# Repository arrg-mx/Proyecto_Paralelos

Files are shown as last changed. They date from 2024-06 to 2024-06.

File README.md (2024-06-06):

# Proyecto_Paralelos
En este repositorio de administrarán los proyectos y sus respectivos programas relacionados con el desarrollo e implementación de robots paralelos por cables.

- [Objetivo](#objetivo)
- [Metas](#metas)
- [Participantes](#participantes)
- [Referencias](#referencias)

## Objetivo

Implementar un robot paralelo dirigido por cables para que este pueda realizar tareas de sensado y manipulación de materiales.

## Metas

- [ ] Implementar el actuador de los cables del robot*
- [ ] Diseñar la estructura y el cuerpo del robot para su implementación en la estructura del espacio de trabajo del tercer piso.

## Participantes

**Integrantes del proyecto:**

| Nombre | Observaciones | Semestre |
| :---| :--- | :--- |
| M.I. Erik Peña Medina | **Responsable** | ---- 
| Braughton Portas Ricardo Alastair | **Participante** | 2024-2 |

## Referencias

### ¿Dónde empezar?

1. **Cable-Driven Parallel Robots**[Libro](https://link.springer.com/content/pdf/10.1007/978-3-319-76138-1.pdf).
2. **Open-Source Planar Cable-Driven Robot**[Repositorio](https://github.com/LionelBirglen/OpenSourcePlanarCableRobot/tree/main)
3. **Modelling and Implementation of Cable Driven Parallel Manipulator System with Tension Control** [Repositorio](https://github.com/siddharthumakarthikeyan/Cable-Driven-Parallel-Robots-CDPR-Modelling)
4. **Accuracy of large-scale cable-driven parallel robot with universal joint pulleys**[Articulo](https://hal.science/hal-03393239/)
5. **Cable Driven Parallel Robot**[Video](https://www.youtube.com/watch?v=cxKAWujUV-c)
6. **Digital design of a сable-driven parallel robot**[Articulo](https://iopscience.iop.org/article/10.1088/1757-899X/945/1/012085/pdf)
7. **A Deployable Cable-Driven Parallel Robot With Large Rotational Capabilities for Laser-Scanning Applications**[Articulo](https://ieeexplore.ieee.org/abstract/document/9076279)
8. **Kinematics of the wire-driven parallel robot MARIONET using linear actuators**[Articulo](https://ieeexplore.ieee.org/abstract/document/4543803)
9. **A Review of Cable-Driven Parallel Robots: Typical Configurations, Analysis Techniques, and Control Methods**[Articulo](https://ieeexplore.ieee.org/abstract/document/9745192)
10. **Design and Development of a New Cable-Driven Parallel Robot for Waist Rehabilitation**[Articulo](https://ieeexplore.ieee.org/abstract/document/8716563)
11. **Design and implementation of a cable-driven parallel robot for additive manufacturing applications**[Articulo](https://www.sciencedirect.com/science/article/abs/pii/S0957415822000964)
## Introducción
El presente proyecto tiene por objetivo el diseño, implementación y control de un robot paralelo controlado por cables para ser instalado en el tercer piso del Centro de Ingeniería Avanzada en la facultad de Ingeniería.
## Etapas de desarrollo
Este proyecto constara de las siguientes etapas de desarrollo las cuales se realizarán de manera secuencial:
1. Diseño y construcción del actuador encargado de la variación de longitud de los cables.
2. Diseño y construcción de la estructura necesaria para soportar el actuador .
3. Implementación del método de control del actuador 
...
## 1. Diseño y constrcción del actuador
Para el diseño del actuador, tras analizar los mecanismos existentes actualmente se optó por un tornillo sin fin el cual cumpla la función de un carrete para el cable conectado directamente a la flecha de un motor pololou GB37-100.  
En esta etapa se realizaron múltiples iteraciones con la finalidad de refinar el diseño.

- **Primera iteración**  
En esta iteración se imprimió el modelo con un relleno de 10% y un espesor de pared de .8mm lo cual hizo que la pieza fuera altamente frágil por lo cual ni siquiera se concluyó la impresión, sin embargo con la parte impresa al retirar los soportes la pieza fracturó reafirmando la observación sobre su fragilidad.
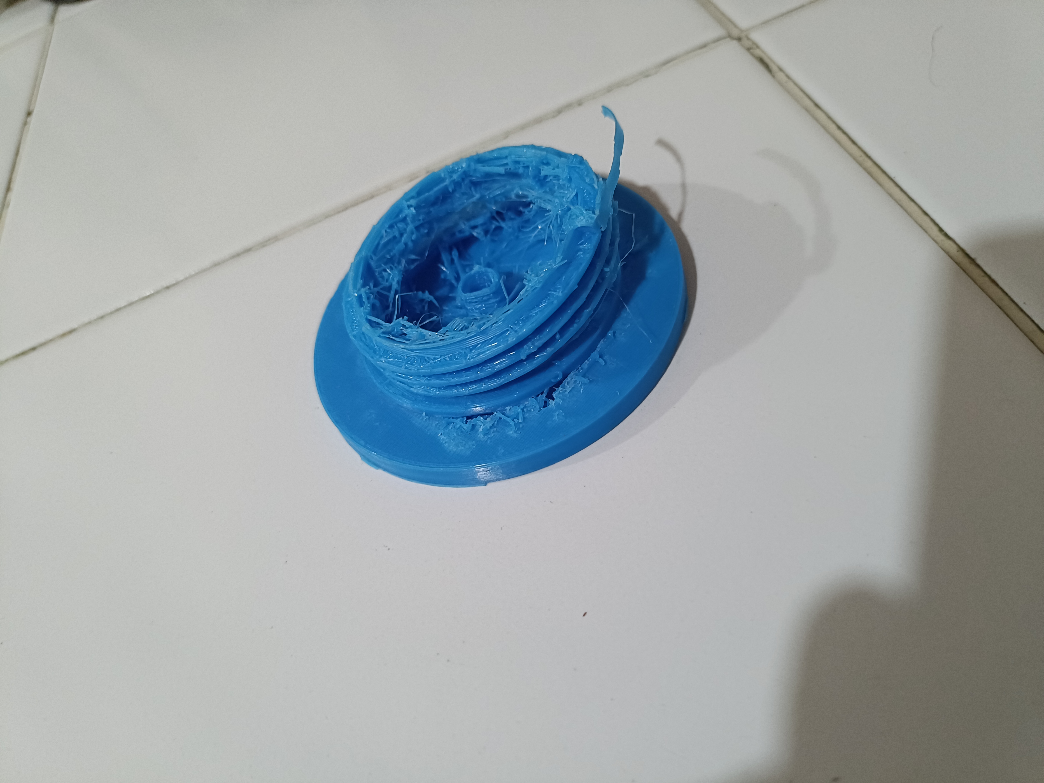
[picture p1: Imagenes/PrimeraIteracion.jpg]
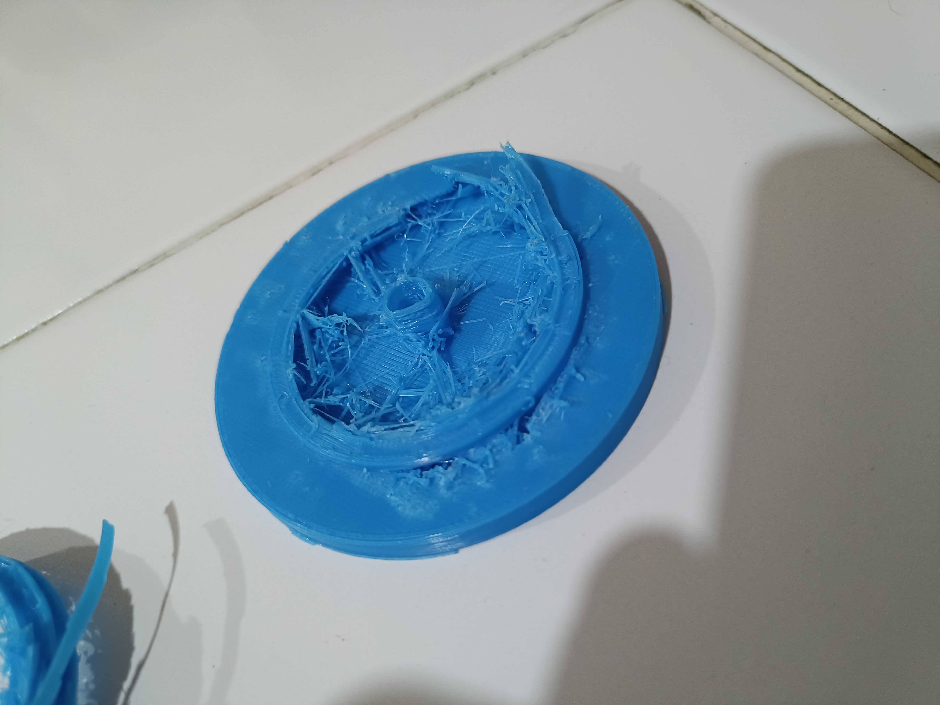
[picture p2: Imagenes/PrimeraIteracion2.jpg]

- **Segunda iteración**  
Para la segunda iteración se incrementó el relleno a un 20% y el espesor de pared a 2mm lo cual generó una pieza exitosa, sin embargo, con esta impresión nos percatamos de que el diseño del carrete no contaba con ninguna clase de soporte, por lo cual, de ser implementado las cargas normales producirían daños en la flecha del motor. Por otro lado, el barreno de la pieza que se diseñó para sostener el hilo se cerró debido a que se diseñó con un grosor muy reducido si embargo este se re-abrió fácilmente con la ayuda de una aguja caliente.
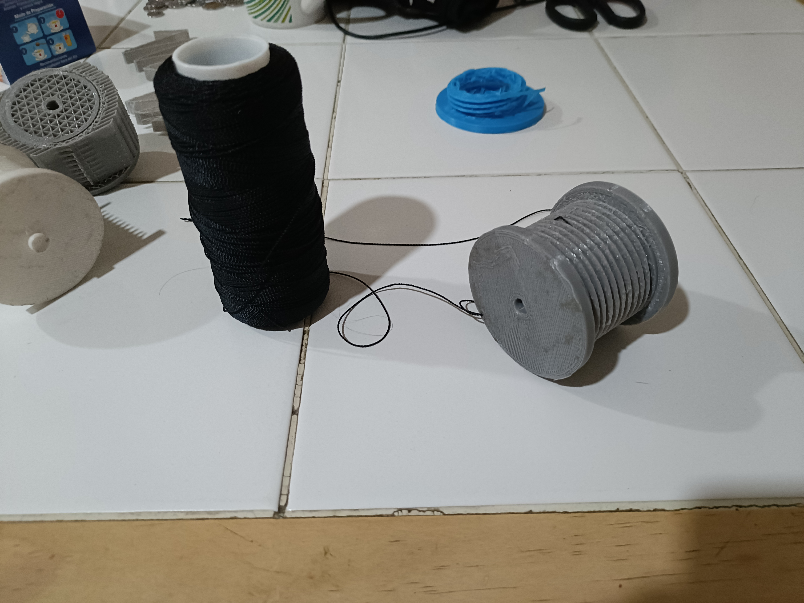
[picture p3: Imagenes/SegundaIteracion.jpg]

- **Tercera iteracion**  
En esta ocasión, tras los errores observados en la impresión pasada, se decidió colocar el carrete sobre un eje acoplado con un balero 608Z.  
Al momento de imprimir esta pieza con los mismos parámetros de impresión de las piezas anteriores, la pieza fallo debido a un corte en el suministro de luz, dejando la pieza a un 80% por lo cual la pieza no fue útil sin embargo se realizaron pruebas de ajuste del eje con el balero, pero al intentar colocar el balero el eje se rompió evidenciando que el diámetro del eje era insuficiente.
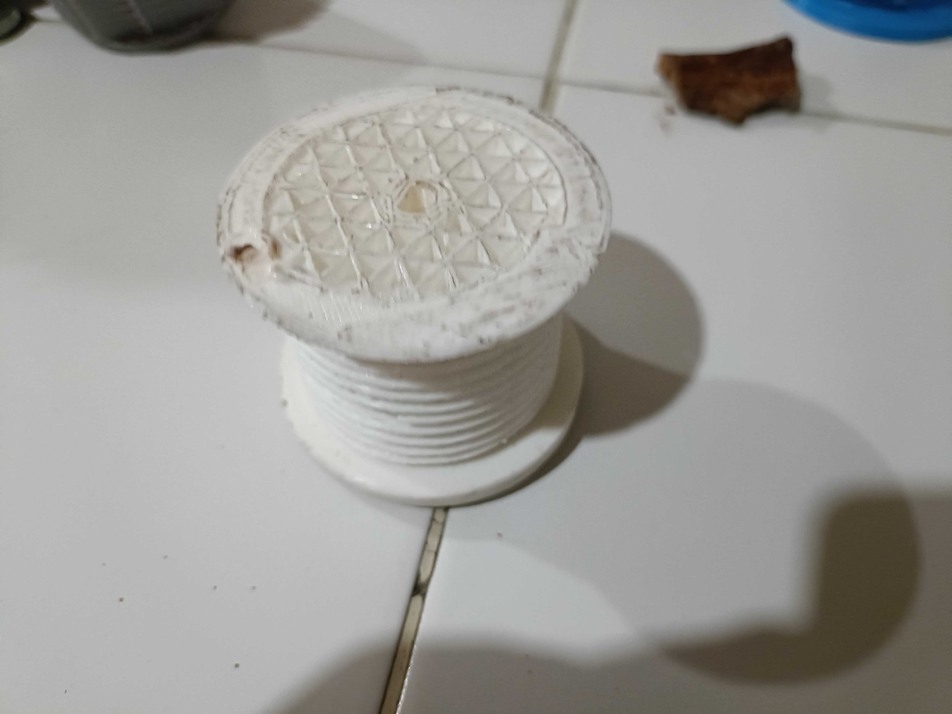
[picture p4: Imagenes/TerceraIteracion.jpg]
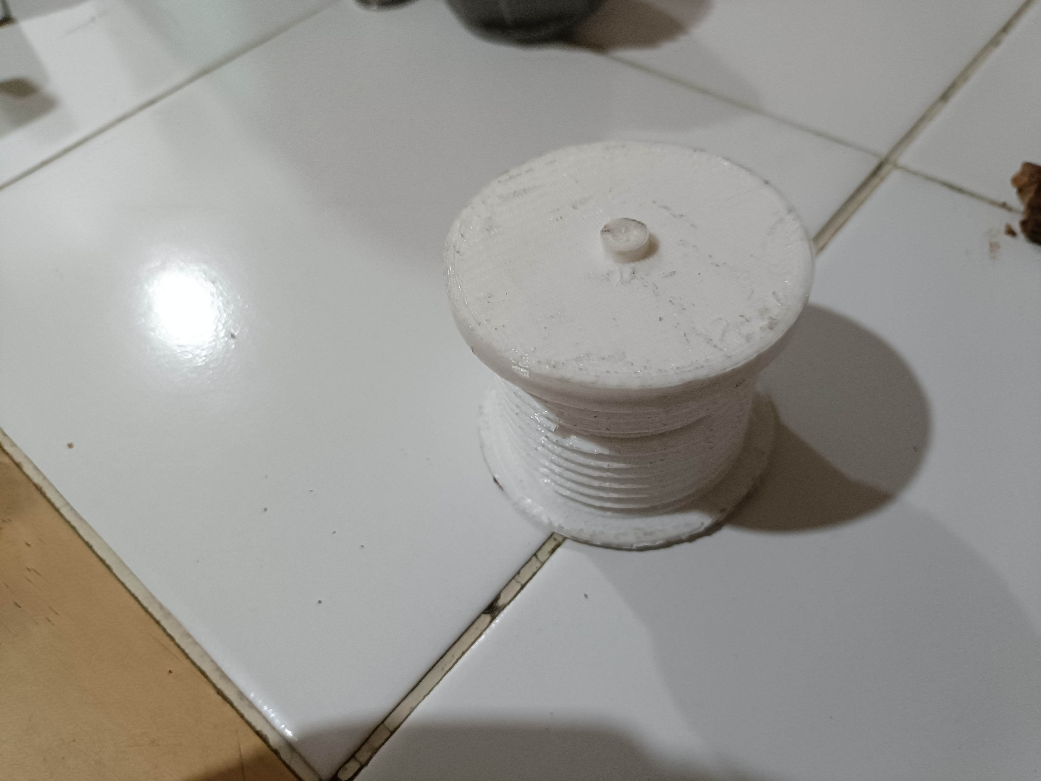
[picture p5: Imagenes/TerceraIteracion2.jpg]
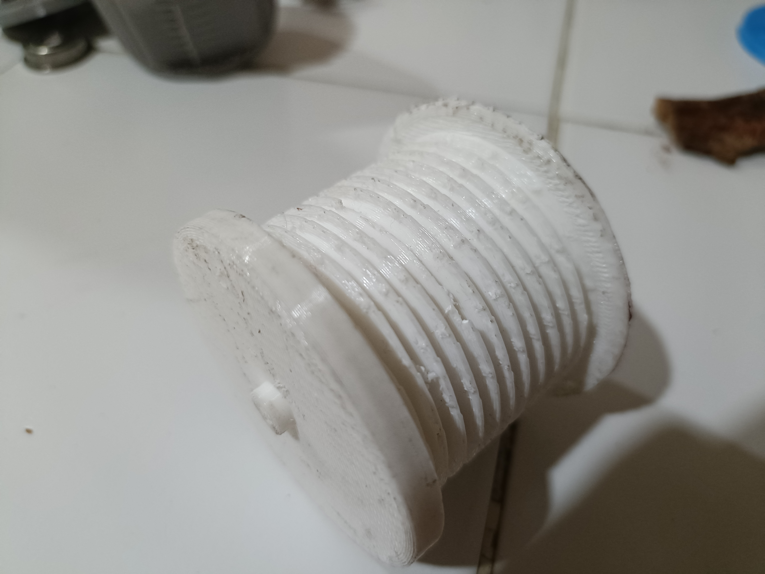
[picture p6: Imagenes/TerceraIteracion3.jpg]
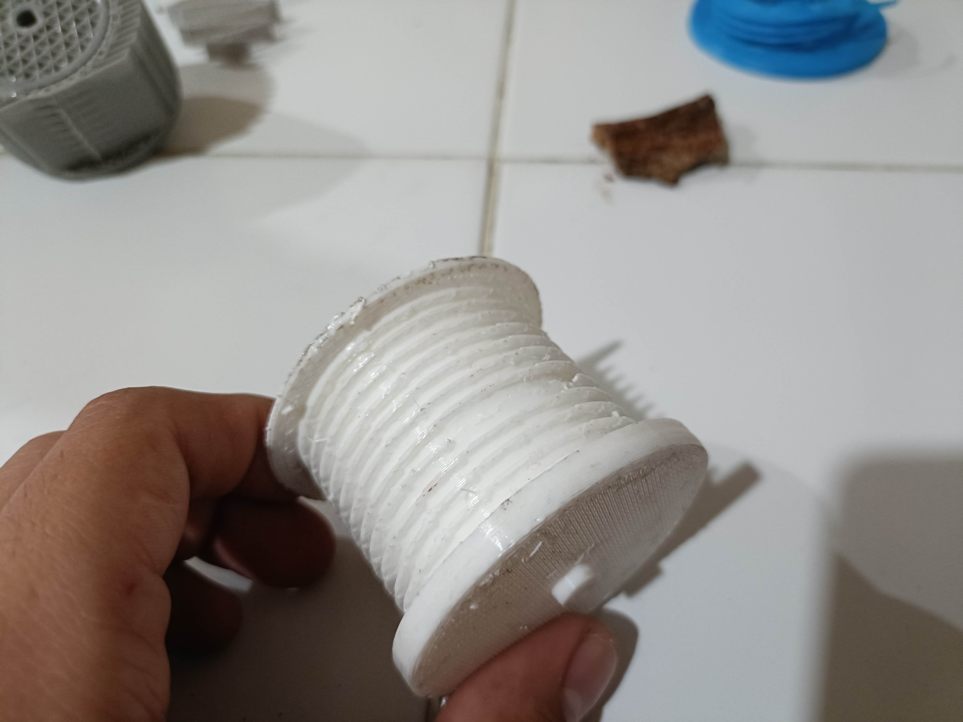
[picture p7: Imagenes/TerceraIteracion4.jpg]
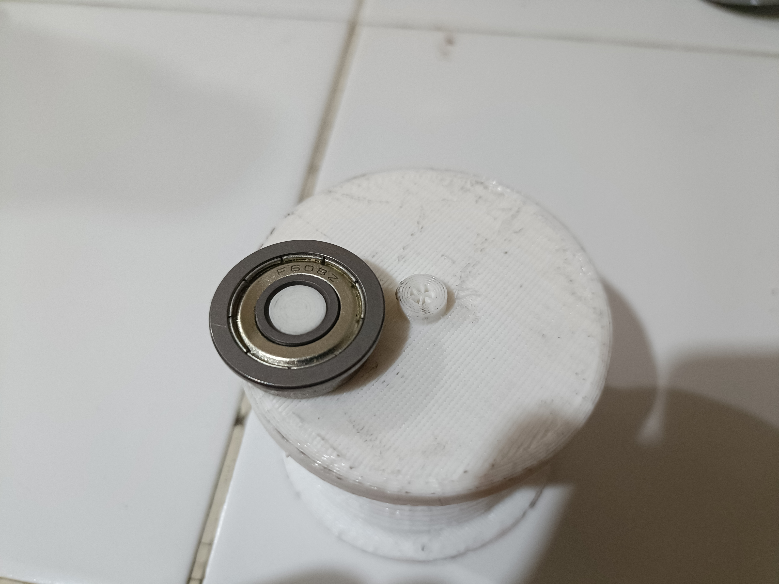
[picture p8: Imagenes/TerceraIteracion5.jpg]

- **Cuarta iteración**  
Para esta iteración se seleccionaron baleros 6201z en los cuales el diámetro interior es un 150% mayor, además se modificaron los archivos de impresión de modo que, aunque la pieza conservaba los parámetros anteriores, en los ejes se aumentó el relleno a un 100% a fin de aumentar la resistencia mecánica. Por desgracia en el proceso de aumentar la densidad se cometió un error en las propiedades de los modelos auxiliares utilizados para modificar la densidad de la pieza haciendo que el eje no fuera impreso correctamente.  
Del mismo modo con base en las iteraciones previas se observó que el espesor de la cuerda del tornillo sin fin era insuficiente lo cual causaba que al retirar los soportes era muy propensa a dañarse o incluso fracturarse, razón por la cual se incrementó el paso de la cuerda.
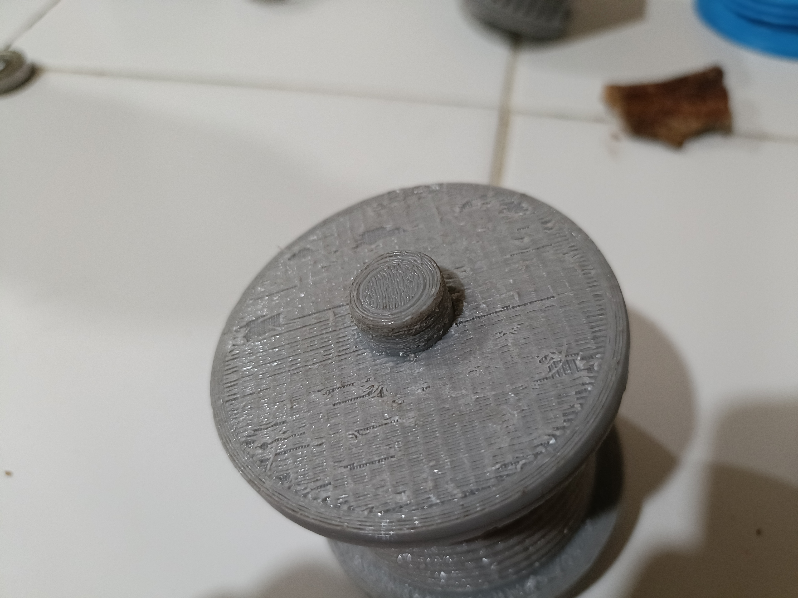
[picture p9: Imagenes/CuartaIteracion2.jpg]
  
- **Quinta iteración**  
Esta iteración volvió a ser incompleta, aunque en esta ocasión se desconoce el motivo, sin embargo, tras un análisis de las partes que si se imprimieron completas, se pudo ver que era necesaria una revisión de las tolerancias en los ejes ya que no presentaban un ajuste adecuado.
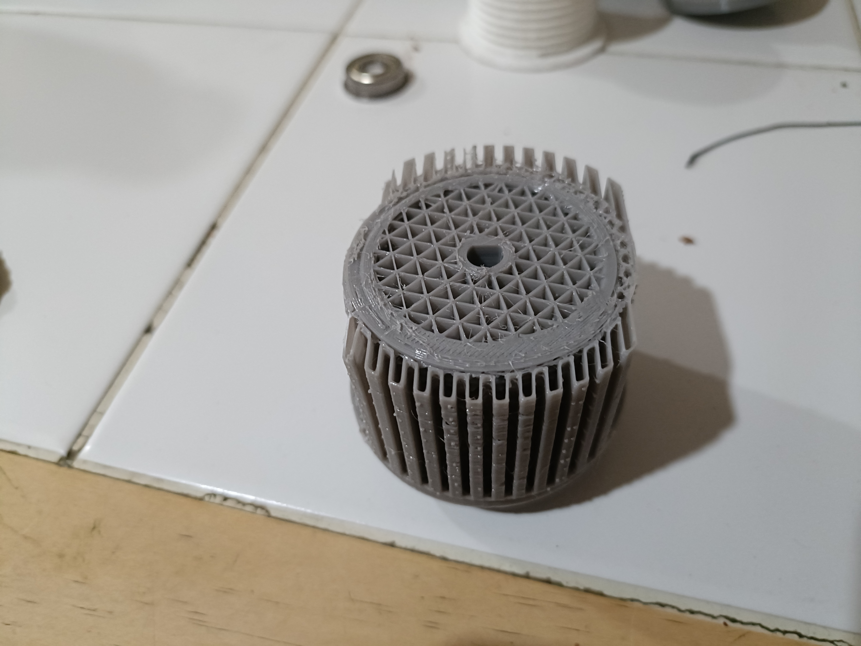
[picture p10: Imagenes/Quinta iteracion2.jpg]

- **Sexta iteración**
Esta fue la última iteración realizada ya que esta ya cuenta con el ajuste de tolerancias y geometría necesaria para el proyecto, los archivos de esta pieza se pueden encontrar en la carpeta de nombre CAD en este mismo repositorio.

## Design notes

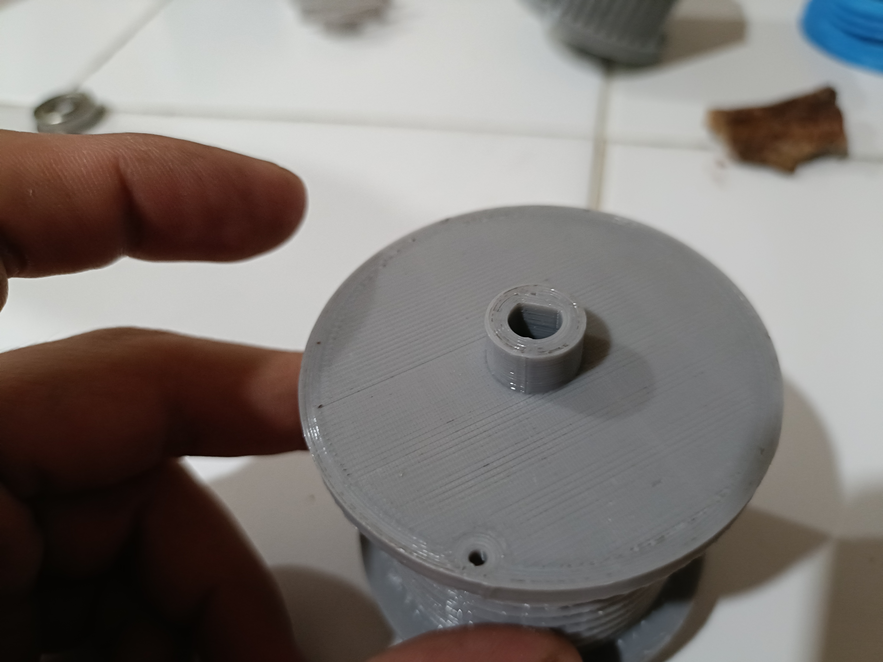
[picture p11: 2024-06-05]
Imagenes/CuartaIteracion3.jpg

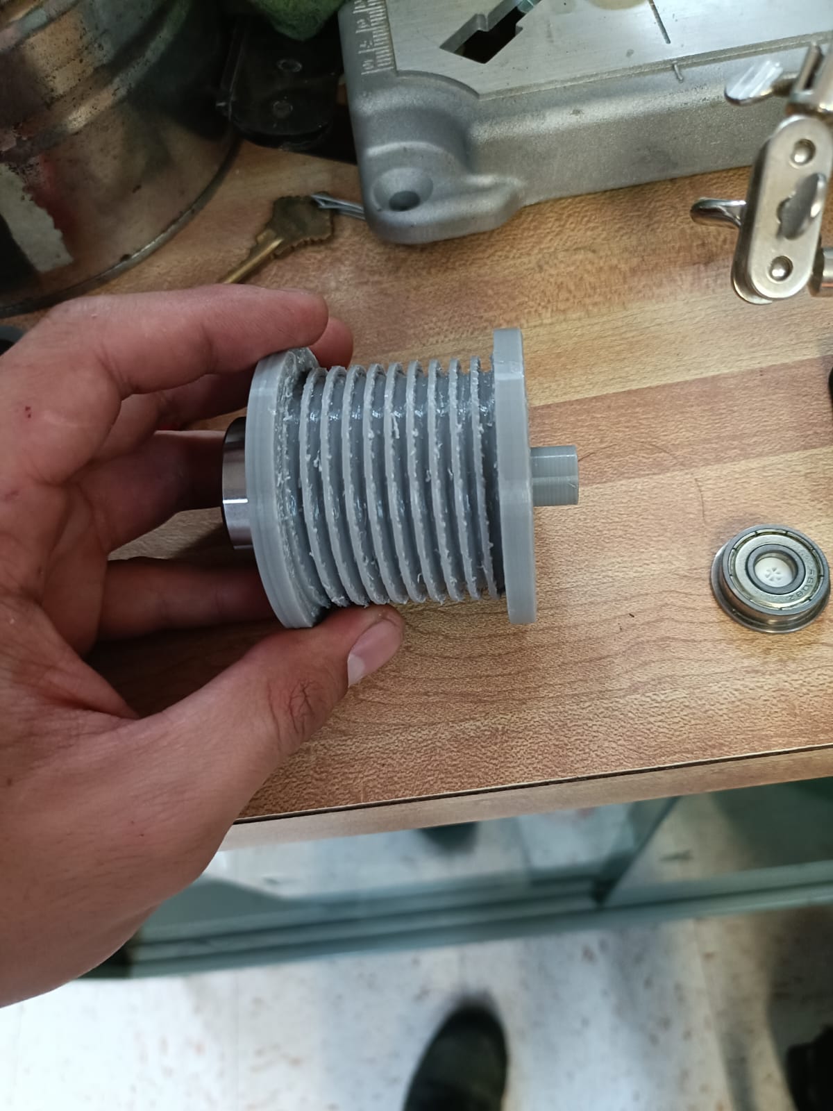
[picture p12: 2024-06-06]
Imagenes/SextaIteracion3.jpg

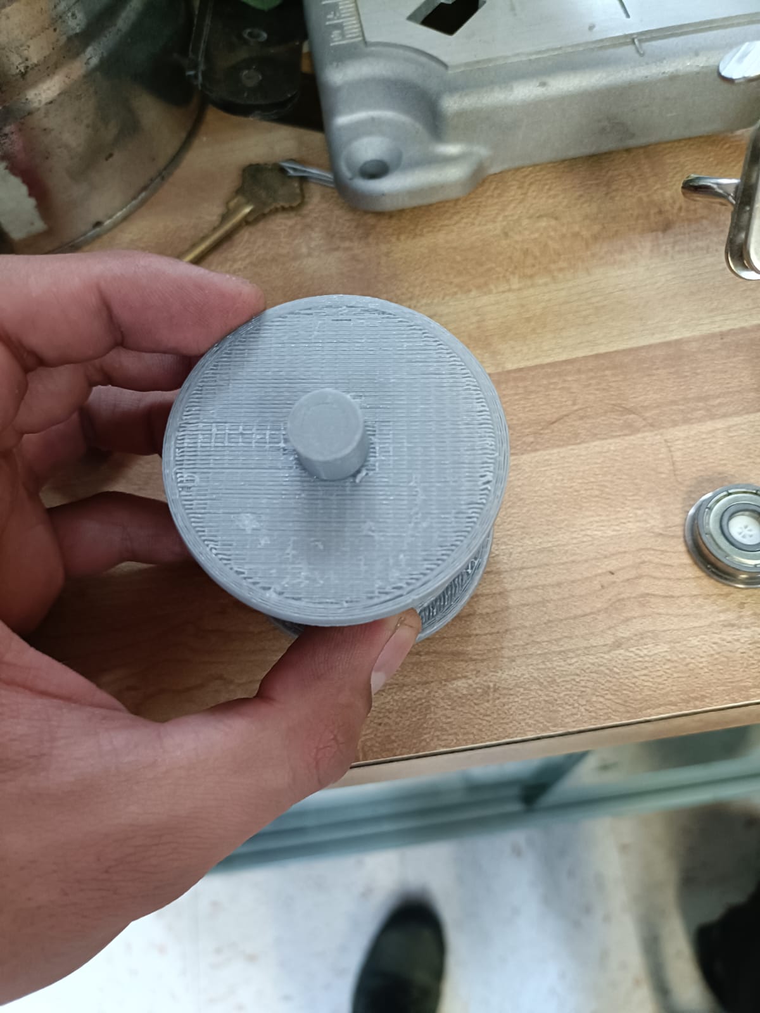
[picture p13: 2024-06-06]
Imagenes/SextaIteracion2.jpg

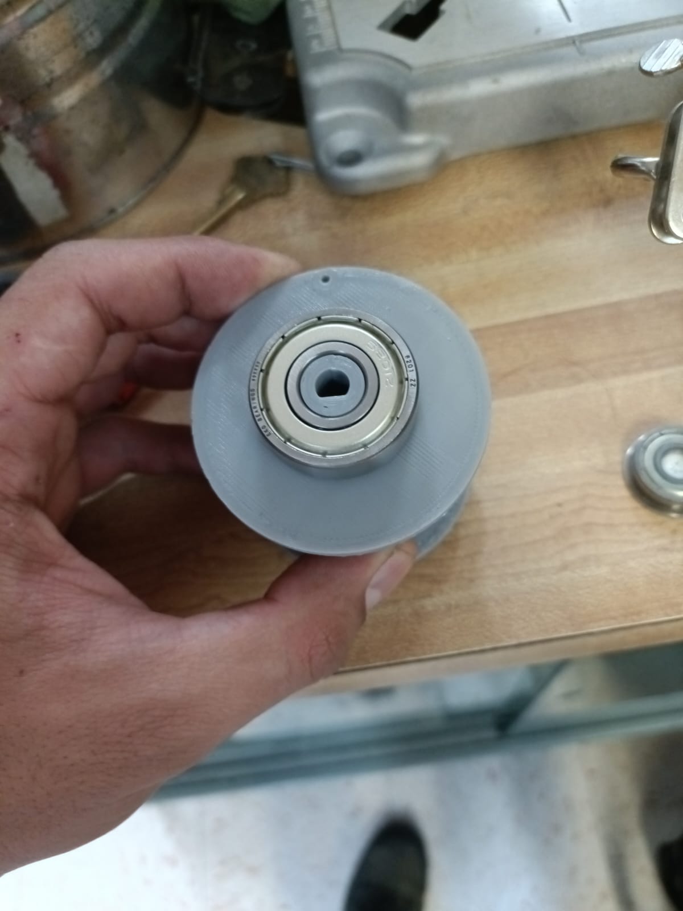
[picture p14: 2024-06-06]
Imagenes/SextaIteracion.jpg

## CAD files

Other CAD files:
CAD/Planos/SoportePared.dwg
CAD/Planos/SoportePoleaInferior.dwg
CAD/Planos/Polea.dwg
CAD/Planos/Prueba eje.dwg
CAD/Planos/SoportePoleaFrontal-1.dwg
CAD/Planos/SoporteBaleroSuperior.dwg
CAD/Planos/SoporteSoporte.dwg
CAD/Planos/SoporteCarrete.dwg
CAD/Planos/Base.dwg
CAD/Planos/CorteParallelRobot.dwg
CAD/Planos/Carrete.dwg
CAD/Ensamble/Ensamblaje proyecto.iam
CAD/Piezas/CarreteAspas ensanchadas.ipt
CAD/Piezas/Polea.ipt
